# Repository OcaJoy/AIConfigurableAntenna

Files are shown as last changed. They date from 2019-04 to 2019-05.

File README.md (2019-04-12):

# AIConfigurableAntenna
The AIConfigurableAtenna is a dipole configruable antenna with 2 reflector antennas. The AIConfigurable Antenna makes use of 2 motors, 1 for extending the main antennas (dipoles) through the use of a belt system, and the other for controlling the distance of the reflector antennas thorugh a gear system. The motors are controlled by an Arduino Mega 2560 REV 3 which is connected to a Raspberry Pi where the AI resides. 

## Documentation
- ReadTheDocs: [https://aiconfigurableantenna.readthedocs.io/en/latest/contents.html](https://aiconfigurableantenna.readthedocs.io/en/latest/contents.html)

## Getting Started

To run this program, the following software are needed:

- [Python](https://www.python.org/downloads/)

- [Arduino](https://www.arduino.cc/en/main/software): is only required to edit and upload the program to the Arduino Mega

## Programs
### ConfigurableAntenna.ino
This is the main Arduino program that will control the length of the antenna depending on the input from RPiArduinoCom.py

### RPiArduinoCom.py
This is the python program that is uploaded to the Raspberry Pi and will be used by the AI to send digital instructions to the Arduino.

## Libraries
- [PySerial](https://pypi.org/project/pyserial/) [Version 3.4]
  - This library is used to establish a serial connection between python and arduino to be able to read and write data between the two systems.
  
- [AccelStepper](https://www.airspayce.com/mikem/arduino/AccelStepper/) [Version 1.59] 
  - This library is used to send signals to the Pololu A4988 Stepper Motor Driver to be able to drive the Stepper Motors.

## Diagrams and Pictures
All diagram and pictures can be found in docs/source/img

## STL CAD Files
All .stl CAD Files can be found in docs/source/slt

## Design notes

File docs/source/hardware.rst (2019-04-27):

Hardware
========

1. Assembly
-----------
1.1. Completed Assembly
^^^^^^^^^^^^^^^^^^^^^^^
This is what a completed assembly looks like

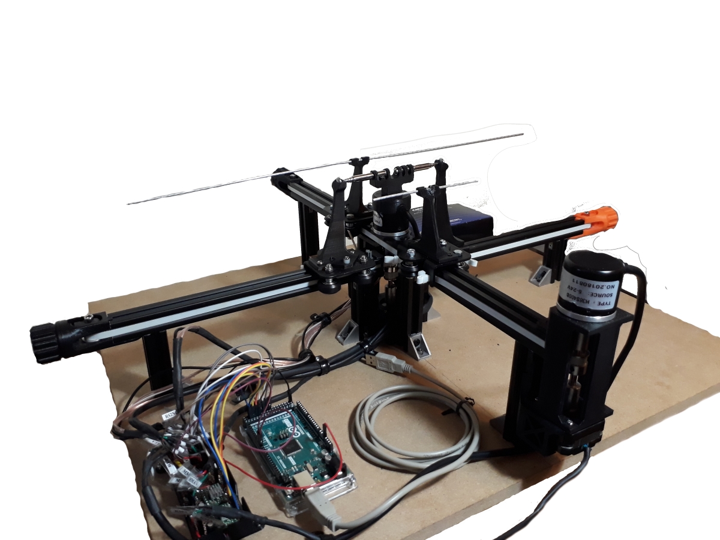
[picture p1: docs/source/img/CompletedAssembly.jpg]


1.2. Assembly Steps
^^^^^^^^^^^^^^^^^^^

2. CAD Files
------------
2.1. Download
^^^^^^^^^^^^^ 
Files can be accessed and downloaded `here <https://github.com/OcaJoy/AIConfigurableAntenna/tree/master/docs/source/slt>`_

2.2. Descriptions
^^^^^^^^^^^^^^^^^

2.2.1. Antenna Holders
~~~~~~~~~~~~~~~~~~~~~~
- Mounting arms that hold the main antenna end for extending and retracting

  | `Antenna_Arms_-_Antenna_support_3-1.STL <https://github.com/OcaJoy/AIConfigurableAntenna/blob/master/docs/source/slt/Antenna%20Holders/Antenna_Arms_-_Antenna_support_3-1.STL>`_
  | `Antenna_Arms_-_Antenna_support_4-1.STL <https://github.com/OcaJoy/AIConfigurableAntenna/blob/master/docs/source/slt/Antenna%20Holders/Antenna_Arms_-_Antenna_support_4-1.STL>`_

- Reflector Antenna holders 

  | `Reflector_support_1.STL <https://github.com/OcaJoy/AIConfigurableAntenna/blob/master/docs/source/slt/Antenna%20Holders/Reflector_support_1.STL>`_

- Central mount that attaches to the top of the center encoder to hold the main anatennas

  | `antenna_center_tall.STL <https://github.com/OcaJoy/AIConfigurableAntenna/blob/master/docs/source/slt/Antenna%20Holders/antenna_center_tall.STL>`_

2.2.2. Bracket Holders
~~~~~~~~~~~~~~~~~~~~~~
- Bracket of Raspberry Pi that can be mounted by sliding in and out of a mounting position

  | `Pi_holder.STL <https://github.com/OcaJoy/AIConfigurableAntenna/blob/master/docs/source/slt/Bracket%20Holders/Pi_holder.STL>`_

- Bracket of HackRF that can be mounted by sliding in and out of a mounting position

  | `hackRF_holder.STL <https://github.com/OcaJoy/AIConfigurableAntenna/blob/master/docs/source/slt/Bracket%20Holders/hackRF_holder.STL>`_

2.2.3. Circuit Case
~~~~~~~~~~~~~~~~~~~
- Bracket of Circuit Case that can be mounted by sliding in and out of a mounting position

  | `Circuit_case_holder.STL <https://github.com/OcaJoy/AIConfigurableAntenna/blob/master/docs/source/slt/Circuit%20Case/Cuircuit_case_holder.STL>`_

- Custom case of PCB

  | `circuit_case.STL <https://github.com/OcaJoy/AIConfigurableAntenna/blob/master/docs/source/slt/Circuit%20Case/circuit_case.STL>`_

2.2.4. Encoder Mounts
~~~~~~~~~~~~~~~~~~~~~
- Reflector Encoder Mount

  | `encoder_mount_3.STL <https://github.com/OcaJoy/AIConfigurableAntenna/blob/master/docs/source/slt/Encoder%20Mounts/encoder_mount_3.STL>`_

- Main Antenna Encoder Mount

  | `encoder_mount_4.STL <https://github.com/OcaJoy/AIConfigurableAntenna/blob/master/docs/source/slt/Encoder%20Mounts/encoder_mount_4.STL>`_

2.2.5. Main Antenna Assembly
~~~~~~~~~~~~~~~~~~~~~~~~~~~~
- These combine to make a fully assembled base of the Main Antenna

  | `Assembled_antenna_2_-_antenna_base-1.STL <https://github.com/OcaJoy/AIConfigurableAntenna/blob/master/docs/source/slt/Main%20Antenna%20Assembly%20Parts/Assembled_antenna_2_-_antenna_base-1.STL>`_
  | `Assembled_antenna_2_-_antenna_base2-1.STL <https://github.com/OcaJoy/AIConfigurableAntenna/blob/master/docs/source/slt/Main%20Antenna%20Assembly%20Parts/Assembled_antenna_2_-_antenna_base2-1.STL>`_
  | `Assembled_antenna_2_-_antenna_base3-1.STL <https://github.com/OcaJoy/AIConfigurableAntenna/blob/master/docs/source/slt/Main%20Antenna%20Assembly%20Parts/Assembled_antenna_2_-_antenna_base3-1.STL>`_
  | `Assembled_antenna_2_-_antenna_base4-1.STL <https://github.com/OcaJoy/AIConfigurableAntenna/blob/master/docs/source/slt/Main%20Antenna%20Assembly%20Parts/Assembled_antenna_2_-_antenna_base4-1.STL>`_
  | `Assembled_antenna_2_-_antenna_base5-1.STL <https://github.com/OcaJoy/AIConfigurableAntenna/blob/master/docs/source/slt/Main%20Antenna%20Assembly%20Parts/Assembled_antenna_2_-_antenna_base5-1.STL>`_
  | `Assembled_antenna_2_-_antenna_base6-1.STL <https://github.com/OcaJoy/AIConfigurableAntenna/blob/master/docs/source/slt/Main%20Antenna%20Assembly%20Parts/Assembled_antenna_2_-_antenna_base6-1.STL>`_
  | `Assembled_antenna_2_-_antenna_base7-1.STL <https://github.com/OcaJoy/AIConfigurableAntenna/blob/master/docs/source/slt/Main%20Antenna%20Assembly%20Parts/Assembled_antenna_2_-_antenna_base7-1.STL>`_
  | `Assembled_antenna_2_-_antenna_nut-1.STL <https://github.com/OcaJoy/AIConfigurableAntenna/blob/master/docs/source/slt/Main%20Antenna%20Assembly%20Parts/Assembled_antenna_2_-_antenna_nut-1.STL>`_

2.2.6. Microphone Holders
~~~~~~~~~~~~~~~~~~~~~~~~~
- Similar to Antenna arms, these parts are for holding the 2 opposite pointing electret microphones in order to scan for sounds and sound origins

  | `mic_support_1.STL <https://github.com/OcaJoy/AIConfigurableAntenna/blob/master/docs/source/slt/Microphone%20Holders/mic_support_1.STL>`_ [Main Antenna Holder] (x1)
  | `mic_support_2.STL <https://github.com/OcaJoy/AIConfigurableAntenna/blob/master/docs/source/slt/Microphone%20Holders/mic_support_2.STL>`_ [Reflector Holders] (x2)
  | `mic_support_3.STL <https://github.com/OcaJoy/AIConfigurableAntenna/blob/master/docs/source/slt/Microphone%20Holders/mic_support_3.STL>`_ [Main Antenna Holder (lowest sitting rail)] (x1)

2.2.7. Microswitch Mounts
~~~~~~~~~~~~~~~~~~~~~~~~~
- These mounts hold the microswitches for homing function 

  | `Microswitch_mount.STL <https://github.com/OcaJoy/AIConfigurableAntenna/blob/master/docs/source/slt/Microswitch%20Mounts/Microswitch_mount.STL>`_ [Holders for Main Antenna Microswitches] (x2)
  | `Microswitch_mount_reflector.STL <https://github.com/OcaJoy/AIConfigurableAntenna/blob/master/docs/source/slt/Microswitch%20Mounts/Microswitch_mount_reflector.STL>`_ [Holders for Reflector Microswitches] (x2)

2.2.8. Motor Holders
~~~~~~~~~~~~~~~~~~~~
- These are for holding the motors in place

  | `motor_bracket_3.STL <https://github.com/OcaJoy/AIConfigurableAntenna/blob/master/docs/source/slt/Motor%20Holders/motor_bracket_3.STL>`_ [Main Antenna Motor Holder]
  | `new_motor_mount.STL <https://github.com/OcaJoy/AIConfigurableAntenna/blob/master/docs/source/slt/Motor%20Holders/new_motor_mount.STL>`_ [Reflector Antenna Motor Holder]

- Main Antenna Motor Brace that mounts the Main Antenna Motor Holder to the rail

  | `motor_bracket_brace.STL <https://github.com/OcaJoy/AIConfigurableAntenna/blob/master/docs/source/slt/Motor%20Holders/motor_bracket_brace.STL>`_

2.2.9. V-Rails
~~~~~~~~~~~~~~
- Longer legs that hold the higher section of the Main Antenna Track

  | `V-Rail_long_leg.STL <https://github.com/OcaJoy/AIConfigurableAntenna/blob/master/docs/source/slt/V%20Rails/V-Rail_long_leg.STL>`_ (x2)

- Shorter legs that hold the lower section of the Main Antenna Track

  | `V-Rail_short_leg.STL <https://github.com/OcaJoy/AIConfigurableAntenna/blob/master/docs/source/slt/V%20Rails/V-Rail_short_leg.STL>`_ (x2)

- V-Rail that the Carriage Plate uses to guide the Main Antennas (27 cm)

  | `V-Rail_track.STL <https://github.com/OcaJoy/AIConfigurableAntenna/blob/master/docs/source/slt/V%20Rails/V-Rail_track.STL>`_ (x2)

- Legs that hold the Reflector Antenna Track and will act as motor and microswitch mounting

  | `V-Rail_Reflector_leg.STL <https://github.com/OcaJoy/AIConfigurableAntenna/blob/master/docs/source/slt/V%20Rails/V-Rail_Reflector_leg.STL>`_ (x4)

- V-Rail that the Carriage Plate uses to guide the Reflector Antennas

  | `V_Rail_track_2.STL <https://github.com/OcaJoy/AIConfigurableAntenna/blob/master/docs/source/slt/V%20Rails/V-Rail_track_2.STL>`_ (x2)

2.2.10. V-Wheel Assembly
~~~~~~~~~~~~~~~~~~~~~~~~
- Creality X Carriage Plate (the plate used by the belt drive on the rail systems to move the antennas)

  | `Creality_X_Carriage_Plate.STL <https://github.com/OcaJoy/AIConfigurableAntenna/blob/master/docs/source/slt/V%20Wheel%20Assembly%20Parts/Creality_X_Carriage_Plate.STL>`_ (x4)

- These parts combines with the Creality X Carriage Plate to create the complete V-Wheel Assembly

  | `assembled_v-wheel_-_bearing-1.STL <https://github.com/OcaJoy/AIConfigurableAntenna/blob/master/docs/source/slt/V%20Wheel%20Assembly%20Parts/assembled_v-wheel_-_bearing-1.STL>`_
  | `assembled_v-wheel_-_bearing-2.STL <https://github.com/OcaJoy/AIConfigurableAntenna/blob/master/docs/source/slt/V%20Wheel%20Assembly%20Parts/assembled_v-wheel_-_bearing-2.STL>`_
  | `assembled_v-wheel_-_spacerexternal-1.STL <https://github.com/OcaJoy/AIConfigurableAntenna/blob/master/docs/source/slt/V%20Wheel%20Assembly%20Parts/assembled_v-wheel_-_spacerexternal-1.STL>`_
  | `assembled_v-wheel_-_spacerinner-1.STL <https://github.com/OcaJoy/AIConfigurableAntenna/blob/master/docs/source/slt/V%20Wheel%20Assembly%20Parts/assembled_v-wheel_-_spacerinner-1.STL>`_
  | `assembled_v-wheel_-_wheel-1.STL <https://github.com/OcaJoy/AIConfigurableAntenna/blob/master/docs/source/slt/V%20Wheel%20Assembly%20Parts/assembled_v-wheel_-_wheel-1.STL>`_

2.2.11. Wiring Channel
~~~~~~~~~~~~~~~~~~~~~~
- Channel that guides small groups of wire into position

  | `Wiring_Channel.STL <https://github.com/OcaJoy/AIConfigurableAntenna/blob/master/docs/source/slt/Wiring_Channel.STL>`_

2.2.12. Rotary Encoder
~~~~~~~~~~~~~~~~~~~~~~
- Stand-in model for the rotary encoders being used

  | `rotary_encoder.STL <https://github.com/OcaJoy/AIConfigurableAntenna/blob/master/docs/source/slt/rotary_encoder.STL>`_ 

3. Electrical Components
------------------------
3.1 Circuit Components
^^^^^^^^^^^^^^^^^^^^^^
- `Pololu A4988 Motor Driver <https://www.pololu.com/product/1182>`_
- `Nema 17 Bi-polar 0.9 Degree Stepper Motor <https://www.omc-stepperonline.com/nema-17-bipolar-09deg-11ncm-156ozin-12a-36v-42x42x21mm-4-wires-17hm08-1204s.html>`_ [17HM08-1204S]
- `Incremental Photoelectric Rotary Encoder 400 P/R <https://www.dfrobot.com/wiki/index.php/Incremental_Photoelectric_Rotary_Encoder_-_400P/R_SKU:_SEN0230>`_ [SEN0230]
- SPDT Omron Microswitch

3.2 Software Defined Radio
^^^^^^^^^^^^^^^^^^^^^^^^^^
- `HackRF One Great Scott Gadgets <https://greatscottgadgets.com/hackrf/one/>`_

3.3 Power Supply
^^^^^^^^^^^^^^^^
- `AC/DC Adadpter - 24VDC 2.5A <https://www.circuittest.com/rpr-2402a5-p5.html>`_ [RPR-2402A5-P5]

4. Circuit Diagrams
-------------------
4.1. Label Definition
^^^^^^^^^^^^^^^^^^^^^
+------------+------------------------------------------------------------+
| Label Name |                         Description:                       |
+============+============================================================+
|    MMA -   | Main Antenna Motor Coil 1 Negative Lead (Black)            |
+------------+------------------------------------------------------------+
|    MMA +   | Main Antenna Motor Coil 1 Positive Lead (Green)            |
+------------+------------------------------------------------------------+
|    MMB +   | Main Antenna Motor Coil 2 Positive Lead (Red)              |
+------------+------------------------------------------------------------+
|    MMB -   | Main Antenna Motor Coil 2 Negative Lead (Blue)             |
+------------+------------------------------------------------------------+
|    RMA -   | Reflector Antenna Motor Coil 1 Negative Lead (Black)       |
+------------+------------------------------------------------------------+
|    RMA +   | Reflector Antenna Motor Coil 1 Positive Lead (Greed)       |
+------------+------------------------------------------------------------+
|    RMB +   | Reflector Antenna Motor Coil 2 Positive Lead (Red)         |
+------------+------------------------------------------------------------+
|    RMB -   | Reflector Antenna Motor Coil 2 Negative Lead (Blue)        |
+------------+------------------------------------------------------------+
|    MEP     | Main Antenna Encoder Power Pin (White)                     |
+------------+------------------------------------------------------------+
|    MEA     | Main Antenna Encoder A Pin (Red)                           |
+------------+------------------------------------------------------------+
|    MEB     | Main Antenna Encoder B Pin (Green)                         |
+------------+------------------------------------------------------------+
|    MEG     | Main Antenna Encoder Ground Pin (Black)                    |
+------------+------------------------------------------------------------+
|    REP     | Reflector Antenna Encoder Power Pin (White)                |
+------------+------------------------------------------------------------+
|    REA     | Reflector Antenna Encoder A Pin (Red)                      | 
+------------+------------------------------------------------------------+
|    REB     | Reflector Antenna Encoder B Pin (Green)                    |
+------------+------------------------------------------------------------+
|    REG     | Reflector Antenna Encoder Ground Pin (Black)               |
+------------+------------------------------------------------------------+
|    MS1NO   | Main Antenna Microswitch 1 Normally Open Contact           |
+------------+------------------------------------------------------------+
|    MS1NC   | Main Antenna Microswitch 1 Normally Closed Contact         |
+------------+------------------------------------------------------------+
|    MS1C    | Main Antenna Microswitch 1 Common Contact                  |
+------------+------------------------------------------------------------+
|    MS2NO   | Main Antenna Microswitch 2 Normally Open Contact           |
+------------+------------------------------------------------------------+
|    MS2NC   | Main Antenna Microswitch 2 Normally Closed Contact         |
+------------+------------------------------------------------------------+
|    MS2C    | Main Antenna Microswitch 2 Common Contact                  |
+------------+------------------------------------------------------------+
|    RS1NO   | Reflector Antenna Microswitch 1 Normally Open Contact      |
+------------+------------------------------------------------------------+
|    RS1NC   | Reflector Antenna Microswitch 1 Normally Closed Contact    |
+------------+------------------------------------------------------------+
|    RS1C    | Reflector Antenna Microswitch 1 Common Contact             |
+------------+------------------------------------------------------------+
|    RS2NO   | Reflector Antenna Microswitch 2 Normally Open Contact      |
+------------+------------------------------------------------------------+
|    RS2NC   | Reflector Antenna Microswitch 2 Normally Closed Contact    |
+------------+------------------------------------------------------------+
|    RS2C    | Reflector Antenna Microswitch 2 Common Contact             |
+------------+------------------------------------------------------------+

4.2. Circuit Schematics
^^^^^^^^^^^^^^^^^^^^^^^

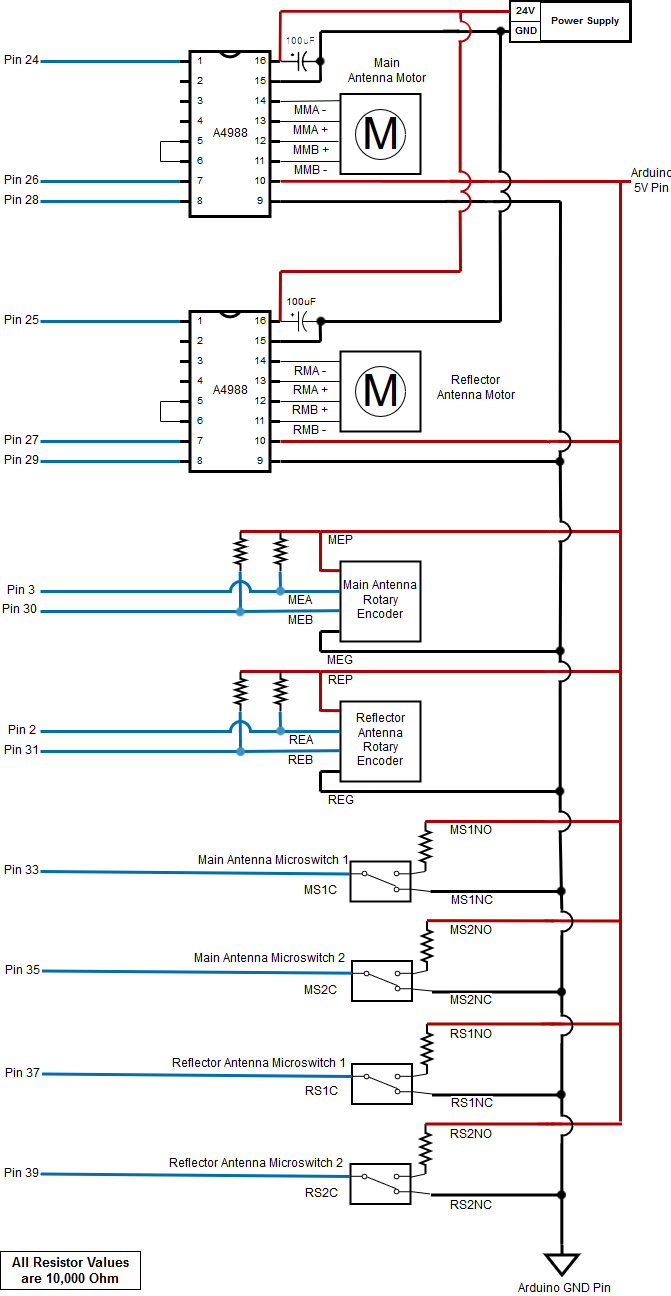
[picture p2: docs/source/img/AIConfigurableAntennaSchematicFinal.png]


4.3. Wiring Diagram
^^^^^^^^^^^^^^^^^^^



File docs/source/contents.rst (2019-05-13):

Welcome to AIConfigurableAntenna's documentation!
=================================================
Description
-----------
The AI Configurable Antenna is a configurable dipole antenna with reflector antennas that are automated by the AI. 

The AI resides in the Raspberry Pi and sends instructions to the Arduino Mega that controls the extension and retraction of the dipole antenna and the reflector antennas. The behavior of the antenna is received through HackRF which is connected to the Raspberry Pi to be analyzed by the AI.
  
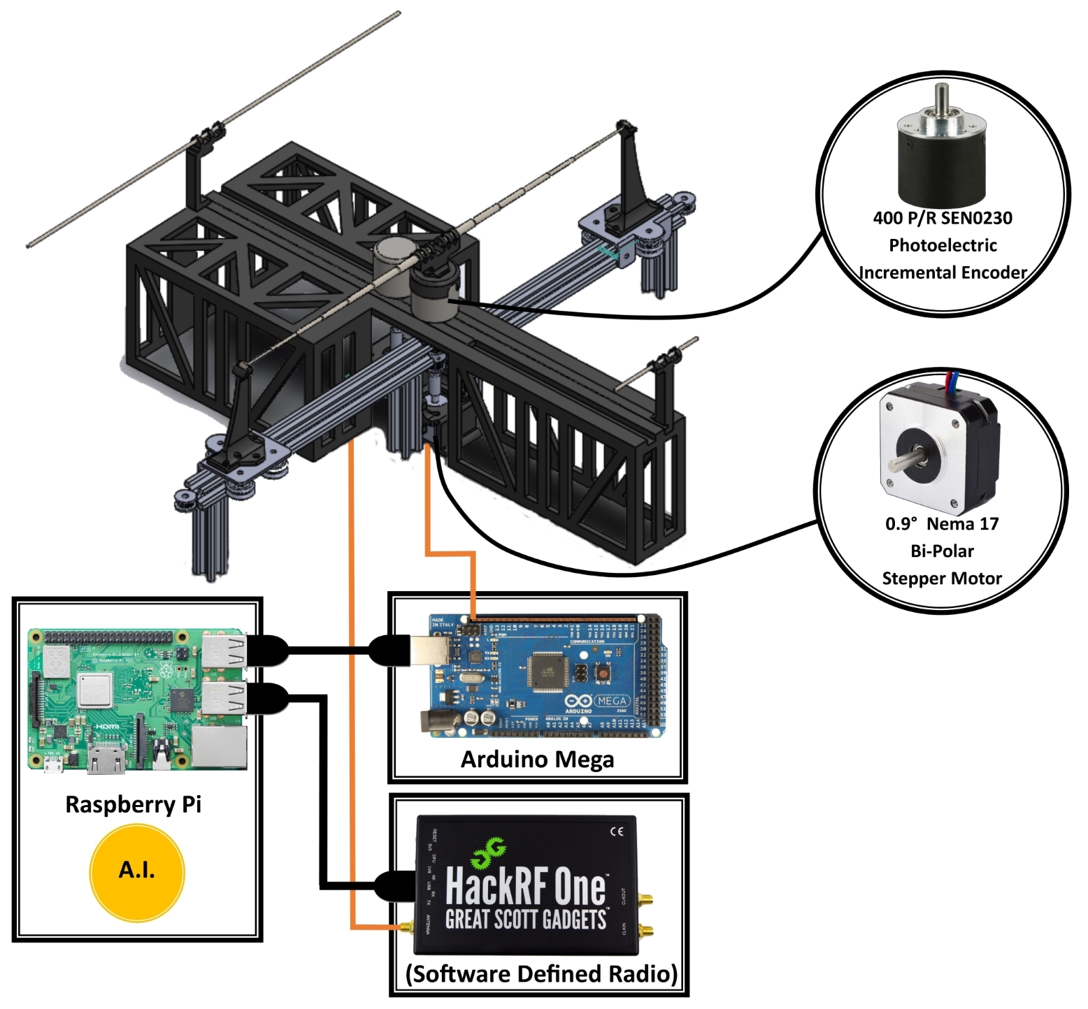
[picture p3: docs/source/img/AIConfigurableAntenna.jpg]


GitHub
------
`https://github.com/OcaJoy/AIConfigurableAntenna <https://github.com/OcaJoy/AIConfigurableAntenna>`_ 

Start Up
--------
1. Connect the power of the circuit board.
2. Connect the Arduino the Raspberry Pi.
3. Run the Raspberry Pi Software. 

Contents
--------

.. toctree::
   :maxdepth: 3
   :glob:
   
   antennaspec
   modesofoperation
   antennaequation
   hardware
   software
   team

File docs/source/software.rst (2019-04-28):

Software
========

1. Getting Started
------------------
| To run this program, the following software are needed:

- `Python <https://www.python.org/downloads/>`_

- `Arduino <https://www.arduino.cc/en/main/software>`_: required to edit and upload the program to the Arduino Mega

2. Libraries
------------
- `PySerial <https://pypi.org/project/pyserial/>`_ [Version 3.4]

  | This library is used to establish a serial connection between python and arduino to be able to read and write data between the two systems.
  
- `AccelStepper <https://www.airspayce.com/mikem/arduino/AccelStepper/>`_ [Version 1.59] 

  | This library is used to send signals to the Pololu A4988 Stepper Motor Driver to be able to drive the Stepper Motors.

3. Raspberry Pi Code (RPiArduinoCom.py)
---------------------------------------
3.0. Install Pyserial
~~~~~~~~~~~~~~~~~~~~~
| To be able to use this program, the Pyserial Library must be pip installed first. Instructions are `here <https://pyserial.readthedocs.io/en/latest/pyserial.html#installation>`_.

3.1. Main Program Description
~~~~~~~~~~~~~~~~~~~~~~~~~~~~~
3.1.1. Setup
^^^^^^^^^^^^
| The program begins by creating a `Serial` object named `arduino` at port `"/dev/ttyACM0"` with a baudrate of 115200. After opening up the specified serial port, the program waits for the Arduino to finish homing the antennas by waiting for a reply. If the reply received from Arduino not code: 02, the program exits.   
| *See the* `5. Communication Codes`_ *section, for more information on what each code mean*

3.1.2. Main Loop
^^^^^^^^^^^^^^^^
| The loop begins by either calling the ``ControlAntenna (modeInput, lengthInput)`` or  the ``HumanInput()`` function to send instructions to the Arduino. When using either of the functions, the user is required to input the desired mode and the desired absolute length of the antenna.  
| *For information on the modes available, see the* :ref:`modesofoperation`.
|
| Once the desired input has been sent, the program waits for a reply from Arduino. The Arduino will then send back data to the Raspberry Pi after it has completed its instruction. The program then reads the reply and determines whether the Arduino successfully performed the instruction or if an error occurred. The last task in the loop is to clear the output buffer to make sure no unintended data will be sent to the Arduino. The program then loops back into asking for another instruction and the cycle continues.   

3.2. Imports
~~~~~~~~~~~~
| Program imports Pyserial to create an object that can serially communicate with the Arduino via USB Cable.  
| ``from serial import Serial``

3.3. Global Variables
~~~~~~~~~~~~~~~~~~~~~
- ``port = "/dev/ttyACM0"``: 

  | Contains the serial port to be communicated with by the `Serial` object

- ``baudrate = 115200`` (int): 

  | Contains the value at which baudrate both devices will serially communicate in

- ``arduino = Serial(port, baudrate)``: 

  | The variable containing the object that opens a serial port at the specified port and baudrate
  | **It is important that this variable is always named "arduino" as the functions:** 
  | **``ControlAntenna(modeInput, lengthInput)``, ``HumanInput()``, ``WaitForArduino()``, and ``CommunicationCode()`` all depend on this variable.**

3.4. Function Definitions
~~~~~~~~~~~~~~~~~~~~~~~~~
3.4.1 ``ControlAntenna(modeInput, lengthInput)``
^^^^^^^^^^^^^^^^^^^^^^^^^^^^^^^^^^^^^^^^^^^^^^^^
- **Description:** 

  | Takes the desired mode and desired absolute antenna length that is inputted in the parameters and sends them to the Arduino; it converts inputs into a string, combines them, and then sends the combined string to the Arduino. 

- **Parameters:** 

  - ``modeInput`` (int): Input an integer from 1-6 to choose a corresponding mode from :ref:`modesofoperation`
  - ``lengthInput`` (int/float): Input the desired length integer or float depending on the mode listed below

    - ``modeInput = 1``: must input a 0
    - ``modeInput = 2``: must input an frequency within 326 MHz to 1.314 GHz (integers only)
    - ``modeInput = 3``: must input the desired absolute length of the main antenna within 5.7 - 23 centimeters
    - ``modeInput = 4``: must input the desired absolute length of the main antenna within 5.7 - 23 centimeters
    - ``modeInput = 5``: must input desired dinstace of main antenna holders from center within 6.7 - 23 centimeters
    - ``modeInput = 6``: must input the desired absolute distance of the reflector antennas within 6.6 - 18.2 centimeters
- **Returns:** None

3.4.2 ``HumanInput()``
^^^^^^^^^^^^^^^^^^^^^^
- **Description:** 

  | Takes a human input via keyboard. This function will check if the values inputted for the desired mode and absolute antenna length are in integers or floats and will keep asking the user to enter again until a valid type is inputted. This function then calls for ``ControlAntenna(modeInput, lengthInput)`` inputting the desired mode to ``modeInput`` and the desired absolute antenna length or frequency to the ``lengthInput``.  
  | This function can be removed when human input is not required.

- **Parameters:** None
- **Returns:** None

3.4.3 ``LengthToSteps(mode, length)``
^^^^^^^^^^^^^^^^^^^^^^^^^^^^^^^^^^^^^^^^^^^^^^^^^^^^^^
- **Description:**

  | This function subtracts the desired absolute length of the antenna with the minimum length of the antenna (`MinMainAntennaLength`) or the minimum distance of the reflector from the main antenna (`MinReflectorAntennaDistance`) depending on the mode chosen to get the remaining distance. The remaining distance is then converted into the targeted steps the motor needs to take by dividing it with the constant ``LengthToStepsConversion``.  
  |
  | This function makes use of these constants internally:
    - ``LengthToStepsConversion = 0.01`` (float): 
   
      | Contains the conversion factor of 0.01 centimeters per 1 step of the motor. The desired absolute length of the antenna inputted is divided by this value to get the number of steps needed by the motor to achieve that length.
    
    - ``MinMainAntennaLength = 5.7`` (float):
  
      | Contains the length of the main antenna at its retracted end position in centimeters. When ``mode = 3 or 4``, this is subtracted from the input to find the distance left needed for the main antenna motor to travel.

    - ``MinMainAntennaHolderDistance = 6.7`` (float):

      | Contains the distance of the main antenna holders from the center at its retracted end position in centimeters. When ``mode = 5``, this is subtracted from the input to find the distance left needed for the main antenna motor to travel.

    - ``MinReflectorAntennaDistance = 6.6`` (float):

      | Contains the distance of the reflector antenna from the main antenna at its retracted end position in centimeters. When ``mode = 6``, this is subtracted from the input to find the distance left needed for the reflector antenna motor to travel.

- **Parameters:**

  - ``mode`` (int): Input the desired mode
  - ``lengthInput`` (int / float): Input the desired absolute length of the antenna
- **Returns:** ``motorSteps`` (int) 

3.4.4. ``WaitForArduino()``
^^^^^^^^^^^^^^^^^^^^^^^^^^^
- **Description:** 

  | This function will check the serial input buffer and will loop doing nothing as long as it is empty. The loop only stops when a reply is received from the Arduino. 

- **Parameters:** None
- **Returns:** None

3.4.5. ``CommunicationCode()``
^^^^^^^^^^^^^^^^^^^^^^^^^^^^^^
- **Description:** 

  | Gets the reply of the Arduino and depending on the code, the program either continues its loop or the program exits.  
  | *See the* `5. Communication Codes`_ *section to see what the the program will perfrom based on the reply.*

- **Parameters:** None
- **Returns:** None

4. Arduino Code (ConfigurableAntenna.ino)
-----------------------------------------
4.1. Main Program Description
~~~~~~~~~~~~~~~~~~~~~~~~~~~~~
4.1.1. Setup
^^^^^^^^^^^^
| Before the main loop of the program begins, the Arduino sets up by determining which of the pins used are inputs and outputs. It then attaches an interrupt to the pins connected to the encoders of the main antennas and reflector antennas. This means that an interrupt will occur when the encoders of the main antennas or the reflector antennas detect a rotation, which will then increment the value that stores how much the motor has rotated in steps. Next, it opens up a serial connection with a baudrate the same as the Raspberry Pi to communicate with it. Lastly, the Arduino homes all the antennas and sends a message to the Raspberry Pi when it is done.

4.1.2. Main Loop
^^^^^^^^^^^^^^^^
| The main loop always checks the serial input buffer if there is a message from the Raspberry Pi. If there is a message, the instruction from the Raspberry Pi is extracted and broken down into two different variables; One variable contains the mode the Arduino will perform, and the other variable contains the frequency desired or the desired step the motor needs to rotate to. The program then performs the mode instructed by the Raspberry Pi.
|
| For modes 2-6, the Arduino will always check if the inputted frequency or length is within the capability of the Configurable Antenna. If it is within its capability, the Arduino does its task and sends a code of "01" back to the Raspberry Pi that it has completed its task and is ready for another one. If it is not within its capability, it sends an error code to the Raspberry Pi.  
| *See the* `5. Communication Codes`_ *section for more information*

4.2. Include
~~~~~~~~~~~~
| The program includes the AccelStepper Library that gives instructions to the motor driver to move the motor.  
| ``#include <AccelStepper.h>``

4.3. Pins
~~~~~~~~~
The value contained is the Arduino Pin Number it is connected to.
 
- ``const int antA_PHASE = 3;``: Pin of the main antenna encoder that triggers the interrupt 
- ``const int antB_PHASE = 30;``: Pin of the main antenna encoder that determines the direction the encoder is revolving in
- ``const int refA_PHASE = 2;``: Pin of the reflector antenna encoder that triggers the interrupt
- ``const int refB_PHASE = 31;``: Pin of the reflector encoder that determines the direction the encoder is revolving in
- ``const int ant_EnaPin = 24;``: Enable pin of the motor driver of the main antenna motor
- ``const int ref_EnaPin = 25;``: Enable pin of the motor driver of the reflector antenna motor
- ``const int ant_StepPin = 26;``: Pin of the motor driver that controls the rotation of the main antenna motor
- ``const int ant_DirPin = 28;``: Pin of the motor driver that controls the rotation direction of the main antenna motor
- ``const int ref_StepPin = 27;``: Pin of the motor driver that controls the rotation of the reflector antenna motor
- ``const int ref_DirPin = 29;``: Pin of the motor driver that controls the rotation direction of the main antenna motor
- ``const int ant1_LimitSwitch = 33;``: Switch that activates when 1st Main Antenna is fully retracted
- ``const int ant2_LimitSwitch = 35;``: Switch that activates when 2nd Main Antenna is fully retracted
- ``const int ref1_LimitSwitch = 37;``: Switch that activates when 1st Reflector Antenna is fully retracted
- ``const int ref2_LimitSwitch = 39;``: Switch that activates when 2nd Reflector Antenna is fully retracted

4.4. Global Variables
~~~~~~~~~~~~~~~~~~~~~
- ``const long freqMIN = 326000000;``: The minimum frequency that the antenna can extend to (320 MHz)

- ``const long freqMAX = 1314000000;``: The maximum frequency that the antenna can shorten to (1.6 GHz)

- ``const int motorSpeed = 1000;``: The speed of the motor in steps per second (with a 400 stepper motor the speed would be 3 revolutions per second)

- ``unsigned long frequency;``: Stores the frequency inputted by the user

- ``String dataInput;``: Contains the combined data taken from the Raspberry Pi for which mode to use and the desired step the motor needs to be

- ``char modeInput;``: Contains the instruction on which mode the Arduino must move the motor in

- ``long ant_ReqStep;``: Contains the required motor steps the main antenna motor needs to move to reach the desired length 

- ``long ref_ReqStep;``: Contains the required motor steps the reflector antenna motor needs to move to reach the desired length

- ``long ant_ENC = 0;``: Contains the main antenna encoder value (Positive values are how many steps the motor has rotated counter-clockwise)

- ``long ref_ENC = 0;``: Contains the reflector antenna encoder value (Positive values are how many steps the motor has rotated counter-clockwise)

- ``float c = 299792458;``: Contains the speed of light in meters, used for calculating the required length of a single dipole with a given frequency

- ``float AntennaLengthMIN = 5.7;``: Contains the minimum length of the main antenna in centimeters

- ``float coversionValue = 0.01;``: Conversion value used to convert the length needed in centimeters to steps needed

4.5. Function Definitions
~~~~~~~~~~~~~~~~~~~~~~~~~
4.5.1. ``EnableMotors(bool state)``
^^^^^^^^^^^^^^^^^^^^^^^^^^^^^^^^^^^
- **Description:** 

  | Enables or disables both the main antenna and reflector antenna motors depending on the inputted `state`. 

- **Parameters:**

  - ``bool state``: an input that determines if both motors are enabled or disabled

    - ``state = 0`` - Enables both motors
    - ``state = 1`` - Disables both motors
- **Returns:** void

4.5.2. ``AntennaHome()``
^^^^^^^^^^^^^^^^^^^^^^^^
- **Description:**
 
  | Moves the main antenna and reflector antennas back to their retracted end position at a lower speed. This function makes use of the inputs of the 4 microswitches: ``ant1_LimitSwitch``, ``ant2_LimitSwitch``, ``ref1_LimitSwitch``, and ``ref2_LimitSwitch`` to check if all the antennas are homed properly.  
  | The homing of the main antenna ends when either one of the main antenna microswitch, ``ant1_LimitSwitch`` or ``ant2_LimitSwitch``, is activated. 
  | The homing of the reflector antenna ends when either one of the reflector antenna microswitch, ``ref1_LimitSwitch`` or ``ref2_LimitSwitch``, is activated. 
  | The function sends a code "02" to the Raspberry Pi when the homing is complete

- **Parameters:** None
- **Returns:** void

4.5.3. ``antEncoder()``
^^^^^^^^^^^^^^^^^^^^^^^
- **Description:** 

  | This function is called when the main antenna encoder triggers an interrupt when it detects a step in the motor. It increases the `long ant_ENC` encoder value by 1 when the motor is stepped once counter-clockwise and decreases the value by 1 when the motor is stepped once clockwise.

- **Parameters:** None
- **Returns:** None

4.5.4. ``refEncoder()``
^^^^^^^^^^^^^^^^^^^^^^^
- **Description:** 

  | This function is called when the reflector antenna encoder triggers an interrupt when it detects a step in the motor. It increases the `long ref_ENC` encoder value by 1 when the motor is stepped once counter-clockwise and decreases the value by 1 when the motor is stepped once clockwise.

- **Parameters:** None
- **Returns:** void

4.5.5. ``StepsCalc(unsigned long freq)``
^^^^^^^^^^^^^^^^^^^^^^^^^^^^^^^^^^^^^^^^
- **Description:** 

  | Calculates the length the main antennas need to extend/retract into based on the frequency inputted by subtracting the main antenna length desired with the main antenna length at minimum frequency. The remaining length, which is the length the main antenna needs to extend/retract into, is converted into motor steps.
- **Parameters:**  

  - ``unsigned long freq``: the frequency the antenna has to shorten/elongate into to tune to
- **Returns:** 

  - ``long steps``: returns the number of steps the main motor antenna needs to be at to achieve the targetted frequency. 

4.5.6. ``MoveMotor(long ReqStep, int Motor, int StepPin, int DirPin)``
^^^^^^^^^^^^^^^^^^^^^^^^^^^^^^^^^^^^^^^^^^^^^^^^^^^^^^^^^^^^^^^^^^^^^^
- **Description:** 

  | Moves the specified motor based on the direction and step pin inputted to the desired steps based on the required steps inputted. The encoder variable is used to check the current position of the antenna to see if it needs to shorten or extend to the required step.   
  | This function uses commands from the `AccelStepper Library <https://www.airspayce.com/mikem/arduino/AccelStepper/classAccelStepper.html>`_ to send instructions to the motor driver to move the motor.

- **Parameters:** 
 
  - ``long ReqStep``: the number of steps the motor is required to move
  - ``int Motor``: determines which encoder value to use 

    - ``Motor = 1`` - Uses Main Antenna Motor Encoder
    - ``Motor = 2`` - Uses Reflector Antenna Motor Encoder
  - ``int StepPin``: the pin of the motor driver that controls the motor 
  - ``int DirPin``: the pin of the motor driver that controls the direction of the motor
- **Returns:** void

5. Communication Codes
----------------------
5.1. Codes
~~~~~~~~~~
The codes that will be sent by the Arduino depending on the success or failure of its performance.

- **00**: ERROR: Mode inputted not valid  

  | This code is sent when the mode inputted is not one of the 5 modes available

- **01**: Antenna ready  

  | This code is sent when the Arduino successfully moved the main antennas and the reflector antennas to the desired length. 

- **02**: Antenna homed  

  | This code is sent when the Arduino successfully homed all the antennas

- **05**: ERROR: Frequency inputted is not within the capability of antennas.  
  | This code is sent to notify that the inputted frequency is not within 326 MHz - 1.314 GHz

- **06**: ERROR: Desired antenna length inputted is not within the capability of antennas.    

  | This code is sent to notify that the inputted antenna length is not within its range 

5.2. How the Arduino sends the codes to the Raspberry Pi
~~~~~~~~~~~~~~~~~~~~~~~~~~~~~~~~~~~~~~~~~~~~~~~~~~~~~~~~
| The Arduino uses the ``Serial.write()`` command to send the code in bytes. The Arduino uses a total of 2 bytes for sending the communication code to the Raspberry Pi.

5.3. How the Raspberry Pi reads the received codes
~~~~~~~~~~~~~~~~~~~~~~~~~~~~~~~~~~~~~~~~~~~~~~~~~~
| The Raspberry Pi uses the ``.read(2)`` command of Pyserial to read the 2 incoming bytes of the communication code. 
| If the Raspberry Pi receives a code that is not 00-06, the Raspberry Pi program exits because there is an unforeseen communication error.

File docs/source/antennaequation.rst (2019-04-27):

Antenna Length Equation
=======================

The Arduino program uses the following equation to calculate the length of a single dipole based on the desired frequency:

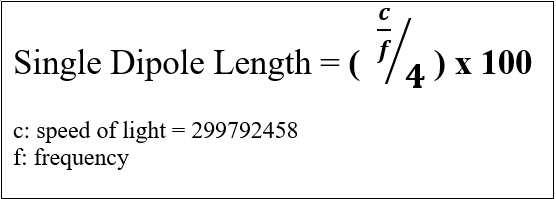
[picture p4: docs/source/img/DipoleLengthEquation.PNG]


(The equation is multiplied by 100 to convert the length from meters to centimeters)

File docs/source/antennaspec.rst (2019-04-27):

Antenna Specification
=====================
- **Main Antenna Length:** 5.7 - 23 cm

- **Reflector Antenna Distance:** 6.6 - 18.2 cm

- **Optimized Frequency Range:** 326 MHz - 1.314 GHz

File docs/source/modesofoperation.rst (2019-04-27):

.. _modesofoperation:

Modes of Operation
==================
- **Mode 1: Home Antennas**
  
  | All antennas are moved back to their retracted end position

- **Mode 2: Move Antennas based on inputted frequency**
  
  | The Main Antennas extend or retract to the desired calculated length based on the inputted frequency. Then, the Reflector Antennas are moved to have their distance match the length of the Main Antennas.
  | The user is required to input a frequency within 326 MHz - 1.314 GHz.

- **Mode 3: Move Antennas to the desired length in centimeters**  

  | The Main Antennas extend or retract to the desired length inputted. Then, the Reflector Antennas are moved to have their distance match the length of the Main Antennas. 
  | The user is required to input the length of a single main antenna between 5.7 - 23 cm.

- **Mode 4: Move only the Main Antennas to the desired length in centimeters** 
 
  | The Main Antennas extend or retract to the desired length inputted. The distance of the Reflector Antennas remains unchanged.
  | The user is required to input the length of a single main antenna between 5.7 - 23 cm.

- **Mode 5: Move only the Main Antenna Holder to the desired distance in centimeters**  

  | The Main Antennas Holders extend or retract to the desired distance from the center inputted. The distance of the Reflector Antennas remains unchanged.
  | The user is required to input the distance of a single main antenna holder from the center between 6.7 - 23 cm

- **Mode 6: Move only the Reflector Antennas to the desired distance in centimeters**

  | The Reflector Antennas extend or retract to the desired distance from the main antennas. The length of the Main Antennas remains unchanged.
  | The user is required to input the distance of the reflector antennas from the main antennas between 6.6 - 18.7 cm.

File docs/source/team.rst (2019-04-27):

The Team
========

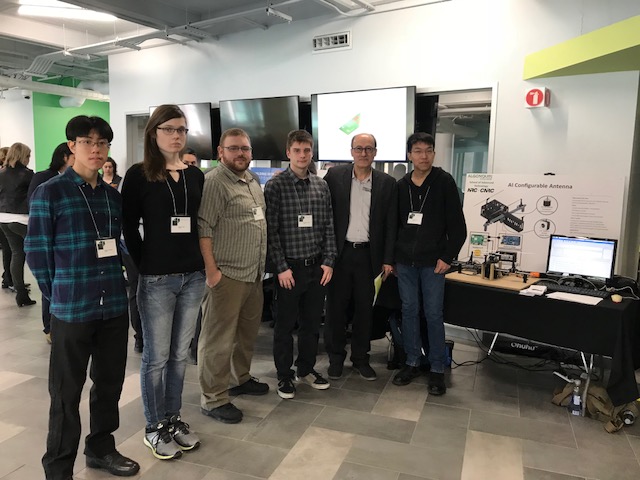
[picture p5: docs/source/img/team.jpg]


In the order from left to right: Johann Ocampo, Bridget Tighe, Glenndyn Foster, Nathaniel Lalonde, Wael Ismael, Junpeng Sun.

Algonoquin Supervising Professor
================================
- Ismael Wael

  - ismaeiw@algonquincollege.com

Contact Info
============
- Glenndyn Foster

  - glennfoster34@gmail.com

- Bridget Tighe

  - B.e.tighe@rogers.com 

- Nathaniel Lalonde

  - nathaniel.lalonde@outlook.com

- Johann Ocampo

  - johannpadraig@yahoo.com

- Junpeng Sun

  - pengyuelei88@163.com

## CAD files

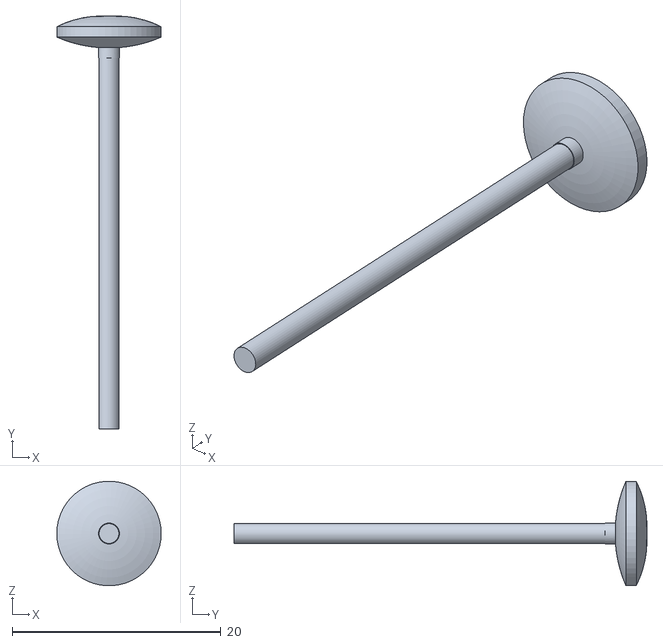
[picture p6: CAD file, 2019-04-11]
docs/source/slt/Main Antenna Assembly Parts/Assembled_antenna_2_-_antenna_base7-1.STL
10.00 x 39.5 x 9.99

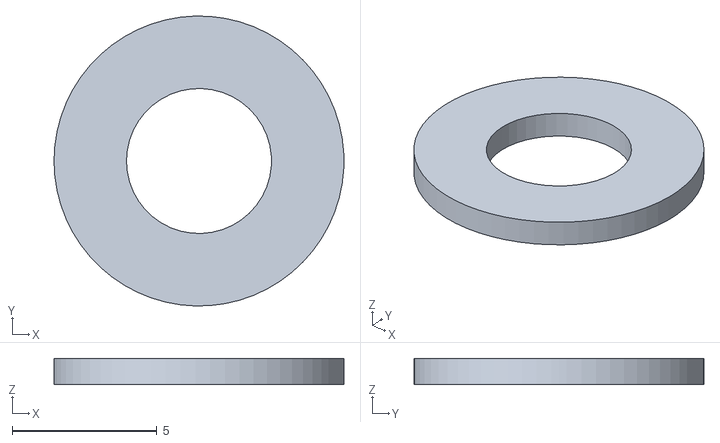
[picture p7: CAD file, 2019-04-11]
docs/source/slt/V Wheel Assembly Parts/assembled_v-wheel_-_spacerinner-1.STL
10.0 x 10.00 x 0.9

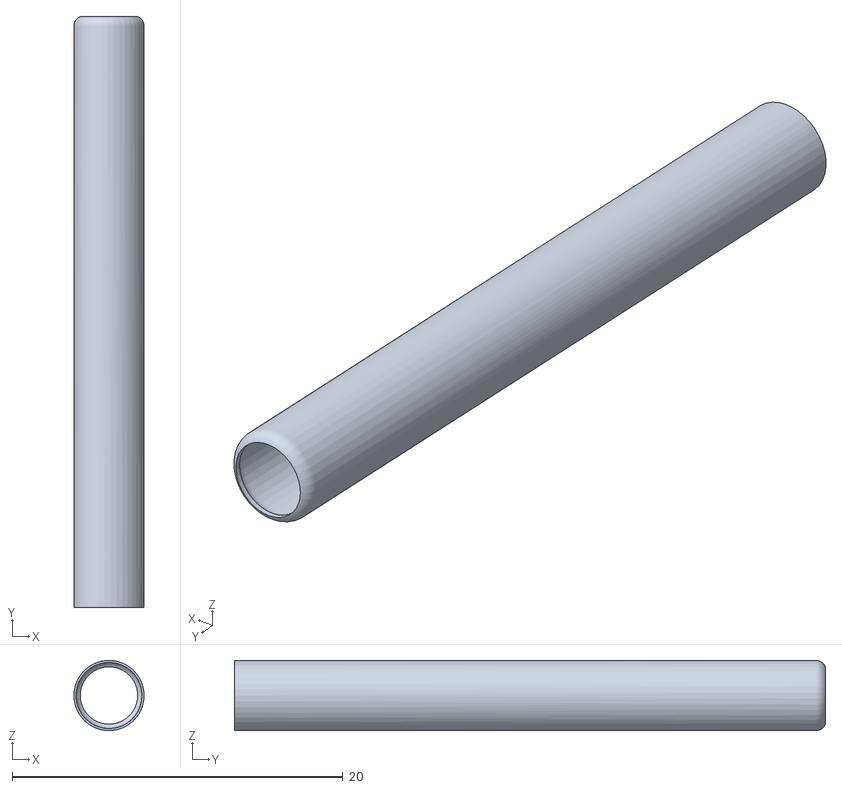
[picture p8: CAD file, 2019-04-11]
docs/source/slt/Main Antenna Assembly Parts/Assembled_antenna_2_-_antenna_base4-1.STL
4.25 x 35.8 x 4.25

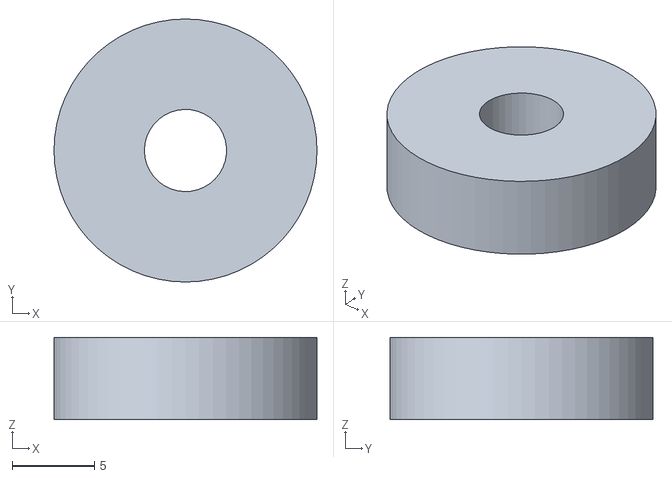
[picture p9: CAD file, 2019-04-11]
docs/source/slt/V Wheel Assembly Parts/assembled_v-wheel_-_bearing-1.STL
16.0 x 16.0 x 5.00

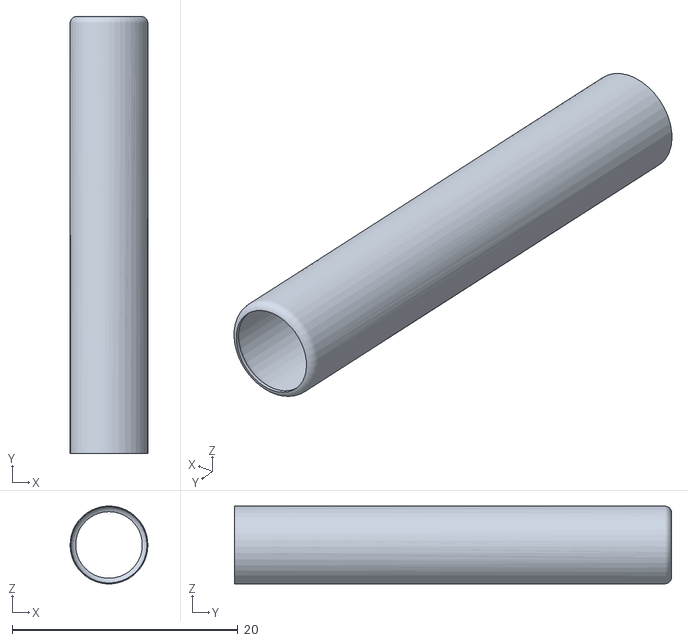
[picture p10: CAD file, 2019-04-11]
docs/source/slt/Main Antenna Assembly Parts/Assembled_antenna_2_-_antenna_base-1.STL
6.90 x 38.8 x 6.90

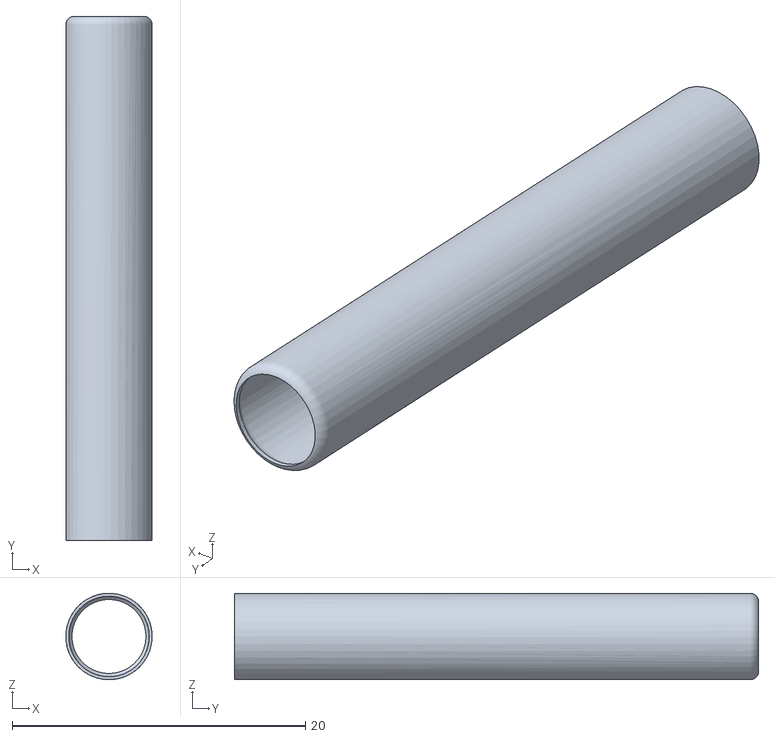
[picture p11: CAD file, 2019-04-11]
docs/source/slt/Main Antenna Assembly Parts/Assembled_antenna_2_-_antenna_base2-1.STL
5.90 x 35.8 x 5.90

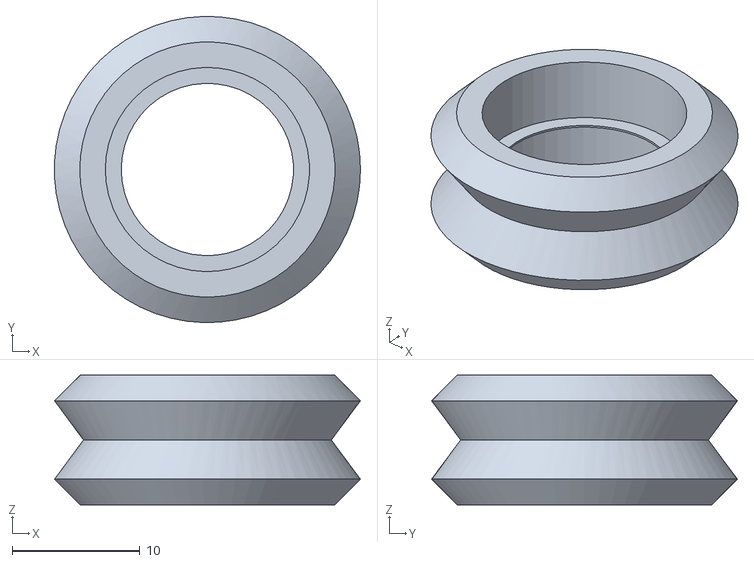
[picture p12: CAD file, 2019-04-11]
docs/source/slt/V Wheel Assembly Parts/assembled_v-wheel_-_wheel-1.STL
24.0 x 24.0 x 10.2

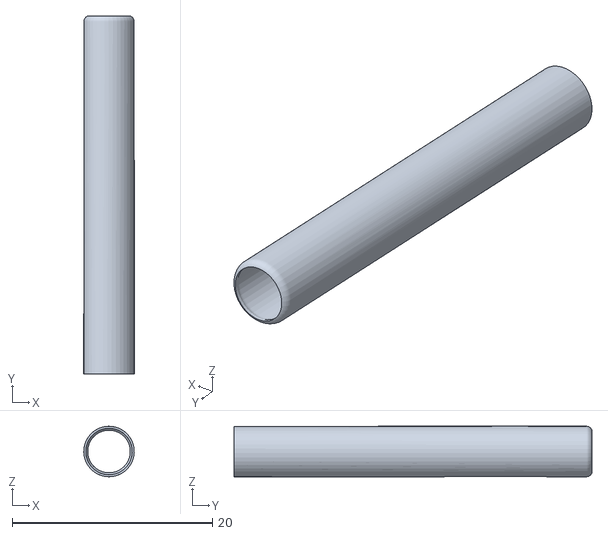
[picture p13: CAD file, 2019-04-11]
docs/source/slt/Main Antenna Assembly Parts/Assembled_antenna_2_-_antenna_base3-1.STL
5.04 x 35.8 x 5.05

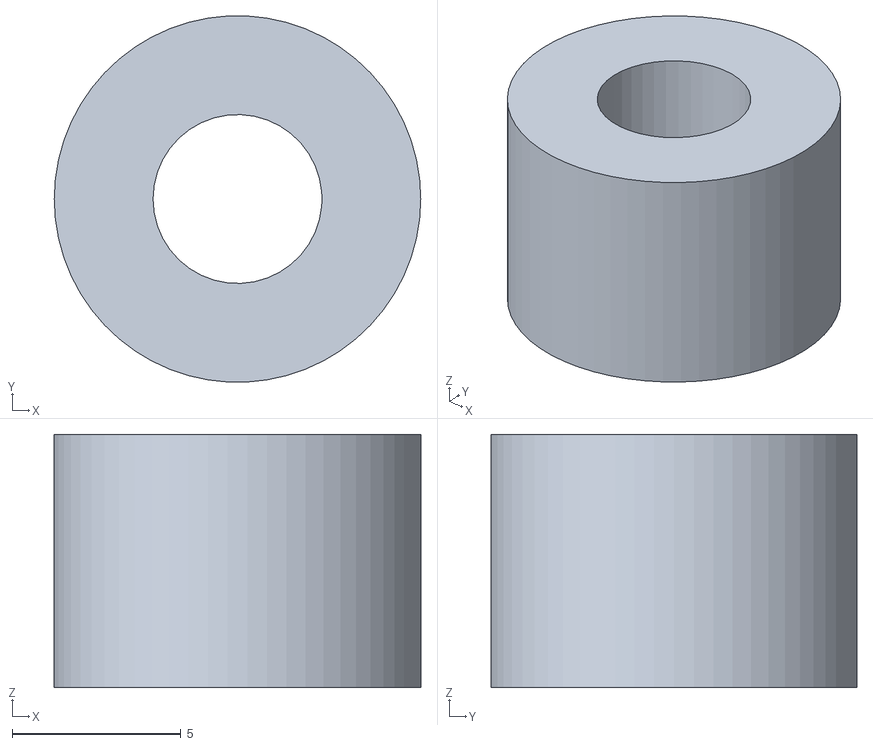
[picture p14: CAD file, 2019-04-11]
docs/source/slt/V Wheel Assembly Parts/assembled_v-wheel_-_spacerexternal-1.STL
10.8 x 10.8 x 7.50

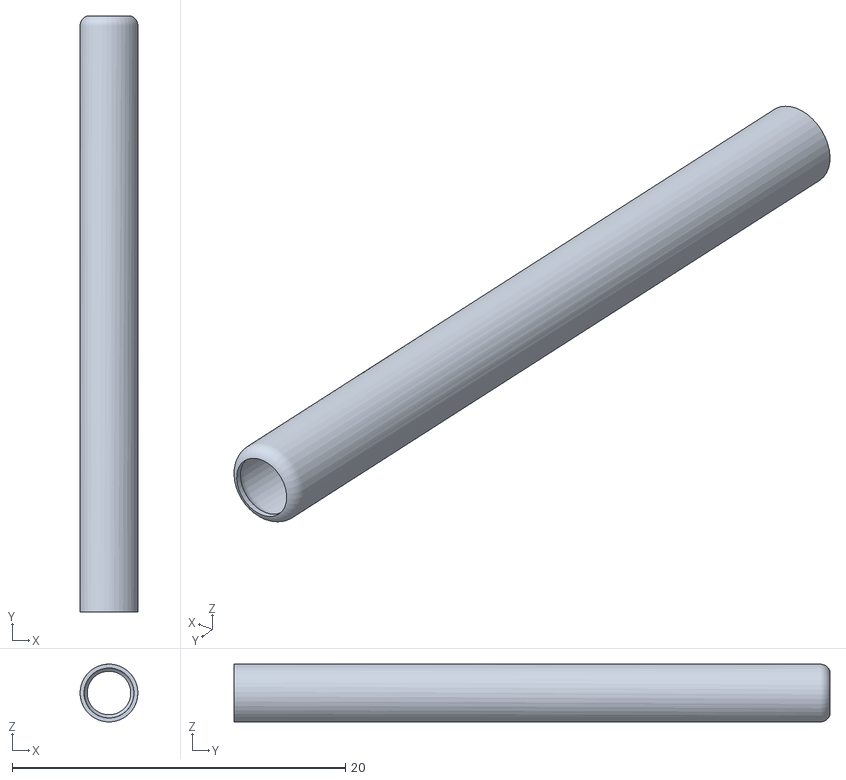
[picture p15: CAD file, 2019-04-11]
docs/source/slt/Main Antenna Assembly Parts/Assembled_antenna_2_-_antenna_base5-1.STL
3.47 x 35.8 x 3.47

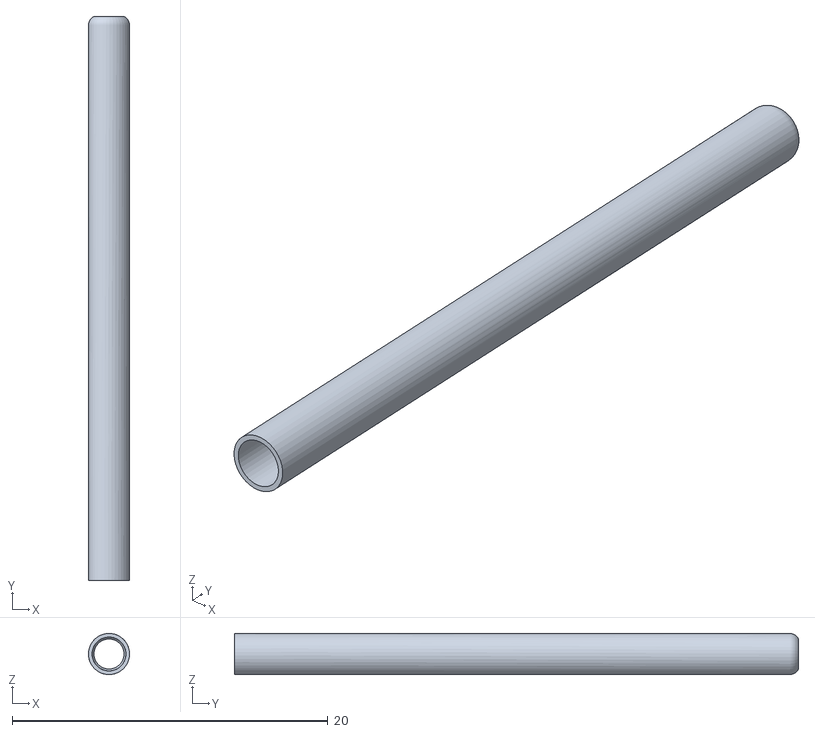
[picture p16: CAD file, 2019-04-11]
docs/source/slt/Main Antenna Assembly Parts/Assembled_antenna_2_-_antenna_base6-1.STL
2.61 x 35.8 x 2.61

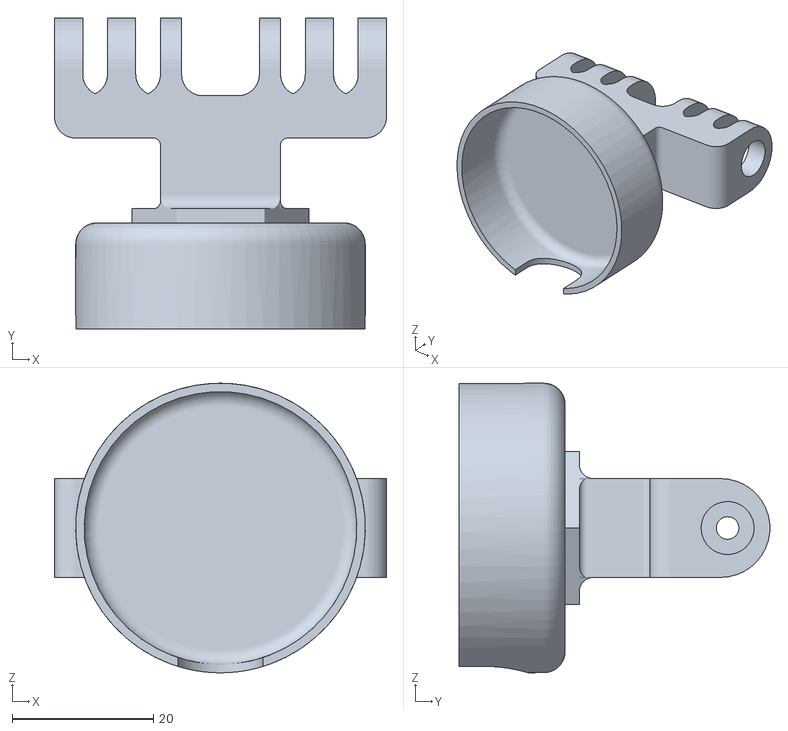
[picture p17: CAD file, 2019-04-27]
docs/source/slt/Antenna Holders/antenna_center_tall.STL
47.0 x 44.0 x 41.0

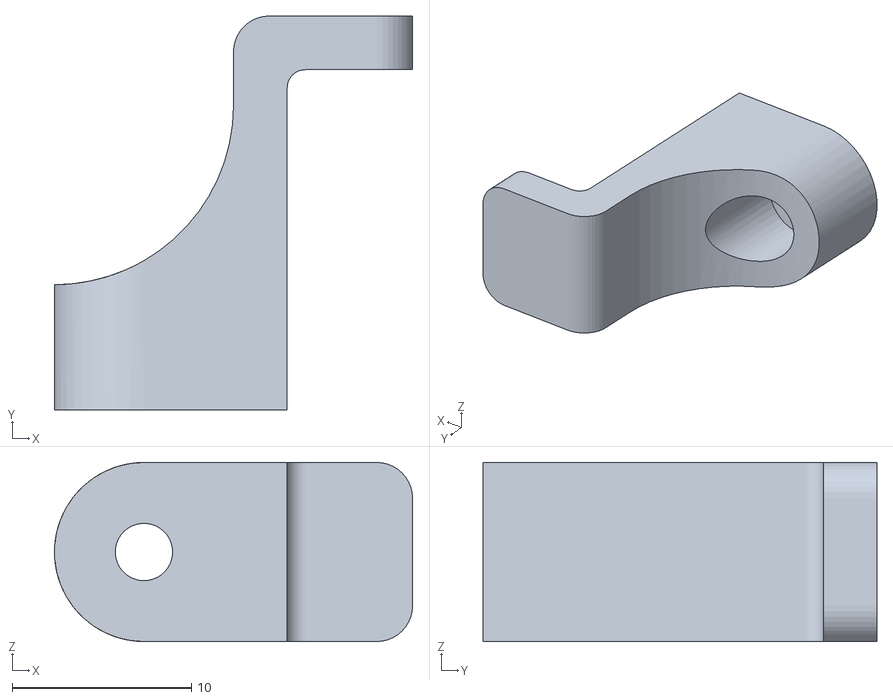
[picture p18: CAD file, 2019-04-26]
docs/source/slt/Bracket Holders/hackRF_holder.STL
20.0 x 22.0 x 10.0

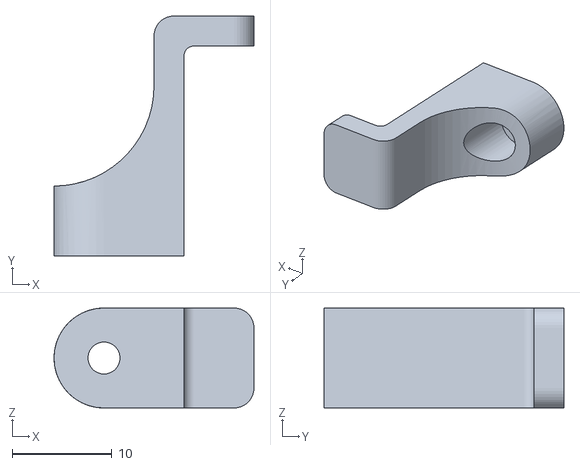
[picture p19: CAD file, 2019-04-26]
docs/source/slt/Circuit Case/Cuircuit_case_holder.STL
20.0 x 24.0 x 10.0

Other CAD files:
docs/source/slt/V Wheel Assembly Parts/assembled_v-wheel_-_bearing-2.STL
docs/source/slt/Encoder Mounts/encoder_mount_3.STL
docs/source/slt/Microphone Holders/mic_support_3.STL
docs/source/slt/Microswitch Mounts/Microswitch_mount_reflector.STL
docs/source/slt/Antenna Holders/Antenna_Arms_-_Antenna_support_3-1.STL
docs/source/slt/Antenna Holders/Antenna_Arms_-_Antenna_support_4-1.STL
docs/source/slt/Antenna Holders/Reflector_support_1.STL
docs/source/slt/Antenna Holders/antenna_mount_and_encoder_cap.STL
docs/source/slt/Bracket Holders/Pi_holder.STL
docs/source/slt/Circuit Case/circuit_case.STL
docs/source/slt/Encoder Mounts/encoder_mount_4.STL
docs/source/slt/Main Antenna Assembly Parts/Assembled_antenna_2_-_antenna_nut-1.STL
docs/source/slt/Microphone Holders/mic_support_1.STL
docs/source/slt/Microphone Holders/mic_support_2.STL
docs/source/slt/Microswitch Mounts/Microswitch_mount.STL
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

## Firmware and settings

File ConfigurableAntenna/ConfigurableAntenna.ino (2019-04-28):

#include <AccelStepper.h>

// Define Constants for Pins
const int antA_PHASE = 3;
const int antB_PHASE = 30;
const int refA_PHASE = 2;
const int refB_PHASE = 31;
const int ant_EnaPin = 24; // Enable pin for Main Antenna Motor
const int ref_EnaPin = 25; // Enable pin for Reflector Antenna Motor
const int ant_StepPin = 26;
const int ant_DirPin = 28;
const int ref_StepPin = 27;
const int ref_DirPin = 29;
const int ant1_LimitSwitch = 33; // Switch that activates when 1st Main Antenna is fully retracted
const int ant2_LimitSwitch = 35; // Switch that activates when 2nd Main Antenna is fully retracted
const int ref1_LimitSwitch = 37; // Switch that activates when 1st Reflector Antenna is fully retracted
const int ref2_LimitSwitch = 39; // Switch that activates when 2nd Reflector Antenna is fully retracted

// Define Min & Max Frequency
const long freqMIN = 326000000; // 326 MHz
const long freqMAX = 1314000000; // 1.314 GHz

// Define Motor Speed
const int motorSpeed = 1000; // in Steps per Second

// Define Global Variables
unsigned long frequency;  // Frequency Variable
String dataInput; //The string of the combined data for which mode to use and the target step the moter needs to be at
char modeInput; // Holds the instruction for which mode to use
long ant_ReqStep; // Required Steps of Antenna Motor
long ref_ReqStep; // Required Steps of Reflector Antenna Motor
long ant_ENC = 0;  // Holds the Main Antenna Encoder Value      (Positive Values are CCW & Negative Valeus are CW)
long ref_ENC = 0;  // Holds the Reflector Antenna Encoder Value 

// Define variables for Caclulating Distance to step
float c = 299792458; // Speed of light in meters
float AntennaLengthMIN = 5.7; // Minimum length of the main antenna in centimeters
float conversionValue = 0.01; // Conversion value used to convert the length needed in centimeters to steps needed

/**********************************************************************************************************************************************************************************               
 * The program sets up by:
 *  - Indicating which pins are inputs and outputs
 *  - Attaching the interrupt function to the encoders
 *  - Opening up a Serial Connection with the Raspberry Pi                
 *  - Homing the antennas on startup 
**********************************************************************************************************************************************************************************/
void setup() {
  // Indicate which pins are inputs and outputs
  pinMode(antA_PHASE, INPUT);
  pinMode(antB_PHASE, INPUT);
  pinMode(refA_PHASE, INPUT);
  pinMode(refB_PHASE, INPUT);
  pinMode(ant1_LimitSwitch, INPUT);
  pinMode(ant2_LimitSwitch, INPUT);
  pinMode(ref1_LimitSwitch, INPUT);
  pinMode(ref2_LimitSwitch, INPUT);
  pinMode(ant_StepPin, OUTPUT);
  pinMode(ant_DirPin, OUTPUT);
  pinMode(ref_StepPin, OUTPUT);
  pinMode(ref_DirPin, OUTPUT);
  pinMode(ant_EnaPin, OUTPUT);
  pinMode(ref_EnaPin, OUTPUT);
  
  // Attach Interrupt to both Rotary Encoders
  attachInterrupt(digitalPinToInterrupt(antA_PHASE), antEncoder, RISING); //Interrupt triggers on Rising Edge
  attachInterrupt(digitalPinToInterrupt(refA_PHASE), refEncoder, RISING); //Interrupt triggers on Rising Edge

  // Set up Serial Connection
  Serial.begin(115200); //Set up the baudrate (has to be the same as what is set on the Raspberry Pi)
  Serial.setTimeout(50);

  // Home the Antennas
  AntennaHome();
}

/*********************************************************************************************************************************************************************************
 * This main function always checks the serial input buffer if there is a message from the Raspberry Pi. 
 * If there is a message, the instructions from the Raspberry Pi is extracted and broken down to read the desired mode and length.
 * The Arduino moves the motor based on the desired inputs.
**********************************************************************************************************************************************************************************/
void loop() {
  // When there is data from Raspberry Pi
  if(Serial.available())
  {
    //Instructions from Raspberry Pi
    dataInput = Serial.readString(); //Get the full instruction from Raspberry Pi and place it in a string
    modeInput = dataInput.charAt(0); // Extract the mode instruction from the first character of the string
    dataInput.remove(0,1); // Remove the first character or the mode instruction from the string

    switch(modeInput)
    {
      // Home Antennas
      case '1': 
        // Home the antennas
        AntennaHome();
        break;

      // Move Antennas to inputted frequency
      case '2': 
        // Convert the dataInput string into an long integer
        frequency = dataInput.toInt();

        if((frequency >= freqMIN) && (frequency <= freqMAX))
        {
          // Calculate required steps needed to reach targetted frequency
          ant_ReqStep = StepsCalc(frequency);

          // Check ant_ReqSteps is between 0-90 steps (5.7 - 6.6 centimeters)
          if((ant_ReqStep >= 0) && (ant_ReqStep <= 90))
          {
            ref_ReqStep = 0; // Reflector Antenna Motor will stay at its minimum distance since it cannot go any lower to match the main antenna's distance
          }
          else if(ant_ReqStep >= 1160) // If ant_ReqSteps is beyond 1210 steps (18.7 centimeters) 
          {
            ref_ReqStep = 1160; // Reflector Antenna Motor will stay at its maximum distance since it cannot go any further to match the main antenna's distance
          }
          else // If the ant_ReqSteps is between 90 - 1210 steps (6.6 - 18.7 centimeters)
          {
            ref_ReqStep = ant_ReqStep - 90; // Decrease the required steps of the Reflector Antenna Motor by 90 steps due to the 0.9 cm difference in minimum distances of the Reflector Antenna and Main Antenna
          }
          
          // Move Antennas
          MoveMotor(ant_ReqStep, 1, ant_StepPin, ant_DirPin);
          MoveMotor(ref_ReqStep, 2, ref_StepPin, ref_DirPin);

          Serial.write("01"); // Send 01: Antenna is at targetted length
        } else {Serial.write("05");} // Send 05: Frequency is not within range
        break;

      // Move Antennas to inputted length
      case '3': 
        // Set the steps needed to reach targetted length
        ant_ReqStep = dataInput.toInt();
        
        // Check ant_ReqSteps is between 0-90 steps (5.7 - 6.6 centimeters)
        if((ant_ReqStep >= 0) && (ant_ReqStep <= 90))
        {
          ref_ReqStep = 0; // Reflector Antenna Motor will stay at its minimum distance since it cannot go any lower to match the main antenna's distance
        }
        else if(ant_ReqStep >= 1160) // If ant_ReqSteps is beyond 1160 steps (18.2 centimeters) 
        {
          ref_ReqStep = 1160; // Reflector Antenna Motor will stay at its maximum distance since it cannot go any further to match the main antenna's distance
        }
        else // If the ant_ReqSteps is between 90 - 1160 steps (6.6 - 18.2 centimeters)
        {
          ref_ReqStep = ant_ReqStep - 90; // Decrease the required steps of the Reflector Antenna Motor by 90 steps due to the 0.9 cm difference in minimum distances of the Reflector Antenna and Main Antenna
        }
        
        // Check if the length input is within the capability of the antenna
        if((ant_ReqStep >= 0) && (ant_ReqStep <= 1730))
        {
          // Move Antennas
          MoveMotor(ant_ReqStep, 1, ant_StepPin, ant_DirPin);
          MoveMotor(ref_ReqStep, 2, ref_StepPin, ref_DirPin);

          Serial.write("01"); // Send 01: Antenna is at targetted length
        } else {Serial.write("06");} // Send 06: Length inputted is outside antenna capability
        break;
        
      // Case 4 & 5 Uses the same instruction as the Raspberry Pi will handle the difference in distancing 
      case '4': // Only move Main Antenna to inputted length
      case '5': // Only move Main Antenna Holders to inputted length from the center
        // Set the steps needed to reach targetted length
        ant_ReqStep = dataInput.toInt();

        // Check if the length input is within the capability of the antenna
        if((ant_ReqStep >= 0) && (ant_ReqStep <= 1730))
        {
          //Move Main Antenna
          MoveMotor(ant_ReqStep, 1, ant_StepPin, ant_DirPin);

          Serial.write("01"); // Send 01: Antenna is at targetted length
        } else {Serial.write("06");} // Send 06: Length inputted is outside antenna capability
        break;

      // Only move Reflector Antenna to inputted length
      case '6':
        //Set the steps needed to reach targetted length
        ref_ReqStep = dataInput.toInt();

        // Check if the length input is within the capability of the antenna
        if((ref_ReqStep >= 0) && (ref_ReqStep <= 1210))
        {
          //Move Main Antenna
          MoveMotor(ref_ReqStep, 2, ref_StepPin, ref_DirPin);

          Serial.write("01"); // Send 01: Antenna is at targetted length
        } else {Serial.write("06");} // Send 06: Length inputted is outside antenna capability
        break;

      default:
        Serial.write("00"); // Send 00: Not a valid mode is given
    }
  }
}

/*********************************************************************************************************************************************************************************
 * Method enableMotors
 *  Enables or disables both motors through the motor driver depending on what is inputted in the parameter "state"
 *  0 - Enables the motor
 *  1 - Disables the motor
 *  
 * Parameter:  bool state - boolean variable that determines if both motors are enabled or disabled
 * Returns: void
**********************************************************************************************************************************************************************************/
void EnableMotors(bool state)
{
  digitalWrite(ant_EnaPin, state);
  digitalWrite(ref_EnaPin, state);
}

/*********************************************************************************************************************************************************************************
 * method antHome
 * Moves the main antenna and reflector antennas back to their retracted end position at a lower speed. 
 * This function makes use of 4 microswitches (2 for the main antennas and the other 2 for the reflector antennas).
 * The homing of the main antenna completes when either of the 2 main antenna microswitch is activated
 * The homing of the reflector antenna completes when either of the 2 reflector antenna microswitch is activated
 * The same logic applies to the microswitches of the reflector antennas.
 * 
 * Parameter:  none
 * Returns:  void
**********************************************************************************************************************************************************************************/
void AntennaHome()
{ 
  // Create AccelStepper Objects
  AccelStepper AntStepper(1, ant_StepPin, ant_DirPin);
  AccelStepper RefStepper(1, ref_StepPin, ref_DirPin);

  // Set max speeds for both motors
  AntStepper.setMaxSpeed(800);
  RefStepper.setMaxSpeed(800);
  
  // Enable both motors
  EnableMotors(0);
  
  // Home the Main Antenna
  while(digitalRead(ant1_LimitSwitch) == LOW  && digitalRead(ant2_LimitSwitch) == LOW) // Motor will continue to retract as long as either switch has not been activated
  {
    AntStepper.move(-90); // Set the motor to move in small steps in the retracting direction
    AntStepper.setSpeed(600); // Set Speed

    // Move the motor
    while(AntStepper.distanceToGo() != 0)
    {
      AntStepper.runSpeedToPosition();
    } 
  }

  // Home the Reflector Antenna
  while(digitalRead(ref1_LimitSwitch) == LOW && digitalRead(ref2_LimitSwitch) == LOW) // Motor will continue to retract as long as either switch has not been activated
  {
    RefStepper.move(-150); // Set the motor to move slowly in the retracting direction
    RefStepper.setSpeed(200); //Set Speed

    // Move the motor
    while(RefStepper.distanceToGo() != 0)
    {
      RefStepper.runSpeedToPosition();
    } 
  }
  
  // Disable both motors
  EnableMotors(1);

  // Set a small delay to make sure motor is at complete stop
  delay(200);
  
  // Reset the Encoder Values
  ant_ENC = 0;
  ref_ENC = 0;
  
  Serial.write("02"); // Send 02: All antennas homed properly
}

/*********************************************************************************************************************************************************************************
 * Method: antEncoder
 * This method is called when the main antenna encoder interrupt is triggered
 * Increases the main antenna encoder value by 1 when encoder is stepped once counter-clockwise and decreases the value by 1 when encoder is stepped once clockwise.
 * 
 * Parameter:  none
 * Returns: void
**********************************************************************************************************************************************************************************/
void antEncoder()
{
  char i;
  i = digitalRead(antB_PHASE);
  if (i==1) // Turning CW
    ant_ENC -= 1;
  else // Turning CCW
    ant_ENC += 1;
}

/*********************************************************************************************************************************************************************************
 * Method: refEncoder
 * This method is called when the reflector antenna encoder interrupt is triggered
 * Increases the main antenna encoder value by 1 when encoder is stepped once counter-clockwise and decreases the value by 1 when encoder is stepped once clockwise.
 * 
 * Parameter:  none
 * Returns: void
**********************************************************************************************************************************************************************************/
void refEncoder()
{
  char i;
  i = digitalRead(refB_PHASE);
  if (i==1) // Turning CW
    ref_ENC -= 1;
  else // Turning CCW
    ref_ENC += 1;
}

/*********************************************************************************************************************************************************************************
 * Method: StepsCalc
 * Calculates the length the main antennas need to shorten or elongate based on the frequency inputted by subtracting the dipole length with the length of the main antenna at minimum frequency
 * 
 * Parameter: unsigned long freq - the frequency the antenna has to tune to
 * Returns: steps - the number of steps the motor has to move to attain the required length
**********************************************************************************************************************************************************************************/
long StepsCalc(unsigned long freq)
{
  float dipoleLength, dipoleLengthToGo;
  long steps;  

  // Calculates the length of a single dipole based on the frequency inputted
  dipoleLength = ((c/freq)/4)*100;
            // Multiplied by 100 to convert meter reading into centimeter 

  // Subtract Antenna Length by Minimum Length
  dipoleLengthToGo = dipoleLength - AntennaLengthMIN; 
  
  // Convert resulting length into # of steps (results are rounded giving an accurasy of above or below 0.005 centimeters)
  steps = round(dipoleLengthToGo/conversionValue);
  
  // Return Steps
  return steps;
}

/*********************************************************************************************************************************************************************************
 * Method: MotorMove
 * Moves the specified motor based on the direction and step pin inputted to the desired steps inputted
 * 
 * Parameter: long ReqStep - the number of steps the motor is required to move
 *            int Motor - determines which encoder variable to use with the motor (should match which motor will be used)
 *                      - Motor = 1: use the Main Antenna Encoder   
 *                      - Motor = 2: use the Reflector Antenna Encoder
 *            int StepPin - the pin of the motor driver that controls the motor
 *            int DirPin - the pin of the motor driver that controls the direction
 * Returns: void
**********************************************************************************************************************************************************************************/
void MoveMotor(long ReqStep, int Motor, int StepPin, int DirPin)
{
  // Create an AccelStepper object that use the inputted Step and Direction Pin of the motor driver specified
  AccelStepper stepper(1, StepPin, DirPin);

  // Set the max speed of the motor
  stepper.setMaxSpeed(motorSpeed);

  // Check if which motor will be used
  if(Motor == 1) // If the Main Antenna Motor is used 
  {
    // Calculate the amount of steps needed to reach the required steps based on the current steps in the Main Antenna Encoder
    stepper.move(ReqStep - ant_ENC);
  }
  else // If the Reflector Antenna Motor is used
  {
    // Calculate the amount of steps needed to reach the required steps based on the current steps in the Reflector Antenna Encoder
    stepper.move(ReqStep - ref_ENC);
  }

  // Set the speed of the motor
  stepper.setSpeed(motorSpeed);

  // Enable Motors
  EnableMotors(0);

  // Keep running motor until the desired step is reached
  while(stepper.distanceToGo() != 0)
  {
    stepper.runSpeedToPosition(); // Command to step motor at constant speed specified
  }

  // Check which Motor is used to determine which Encoder should be used for the closed loop correction of the motor chosen
  if(Motor == 1)
  {
    // Match Main Antenna Encoder reading to required steps
    while(ant_ENC != ReqStep)
    {
      stepper.move(ReqStep - ant_ENC);
      stepper.setSpeed(800);  // Set at lower speed for precise movements

      while(stepper.distanceToGo() != 0)
      {
        stepper.runSpeedToPosition();
      }
    }
  }
  else
  {
    // Match Reflector Encoder reading to required step
      while(ref_ENC != ReqStep)
    {
      stepper.move(ReqStep - ref_ENC);
      stepper.setSpeed(800);  // Set at lower speed for precise movements

      while(stepper.distanceToGo() != 0)
      {
      stepper.runSpeedToPosition();
      }
    }
  }
  
  // Disable Motors:
  EnableMotors(1);
}

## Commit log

2019-03-25 ConfigurableAntenna.ino - added motor move logic - added min & max frequency - updated RPi & Arduino communication Code Number
    RPiArduinoCom.ino
    - updated RPi & Arduino communcation Code Number
    RPiArduinoCom.py
    - updated RPi & Arduino communication Code Number
2019-03-29 Updated RPiArduinoCom.py & ConfigurableAntenna.ino - added 5 modes 1. Homes the Antenna 2. Moves both Antennas based on the frequency inputted 3. Moves both Antennas based on the targetted absolute l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
2019-03-30 Improved RPiArduinoCom code and documentation Updated README with antenna specs
2019-03-31 Updated conversion value and minimum antenna lengths of the antennas for both programs
2019-03-31 Added out of antenna capability check in the arduino file
2019-03-31 Created a communication function in RPiArduinoCom Instead of homing the antenna in the set up of the Arduino, the raspberry sends an instruction homing before proceeding to its main loop
2019-04-01 Modified the files to havingthe antenna home in the set up of the Arduino Code
2019-04-01 Removed the specs of the antenna
2019-04-01 Added more comments on the setup of the Arduino Modified some comments in the RPiArduinoCom for readability
2019-04-11 Improved Arduino and Raspberry Code
2019-04-11 Updated Documentation
    [Antenna_Arms_-_Antenna_support_3-1.STL, Antenna_Arms_-_Antenna_support_4-1.STL, Assembled_antenna_2_-_antenna_base-1.STL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]
2019-04-26 Updated the slt folder structure and models
    [Antenna_Arms_-_Antenna_support_3-1.STL, Antenna_Arms_-_Antenna_support_4-1.STL, Assembled_antenna_2_-_antenna_base-1.STL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]
2019-04-27 Updated Antenna Specs and overall documentation
2019-04-27 Updated antennaspec.rst
2019-04-27 Updated all content
    [antenna_center_tall.STL]
2019-04-28 Updated Homing Function
